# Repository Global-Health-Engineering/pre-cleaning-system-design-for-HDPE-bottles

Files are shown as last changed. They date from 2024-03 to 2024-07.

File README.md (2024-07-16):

<!-- badges: start -->


<!-- badges: end -->

<h1> Design of an HDPE bottle collection and pre-cleaning system for recycling in Blantyre, Malawi </h1>

<b>Contributors</b>  
- Timo Stutz *author*  
- Elizabeth Tilley <a href="https://orcid.org/0000-0002-2095-9724">
ORCID logo 0000-0002-2095-9724
</a> *supervisor*  
- Lin Boynton <a href="https://orcid.org/0000-0002-9944-3834">
ORCID logo 0000-0002-9944-3834
</a> *supervisor*  
- Jakub Tkaczuk <a href="https://orcid.org/0000-0001-7997-9423">
ORCID logo 0000-0001-7997-9423
</a> *supervisor, developer, maintainer*  
- Nicolas Seemann-Ricard <a href="https://orcid.org/0000-0002-0945-7475">
ORCID logo 0000-0002-0945-7475
</a> *developer*  

<br>
<p align="middle"> 

<br><br>
This work is certified by the Open Source Hardware Association.<br \>

<br>
<b>Complete description of system design, functionalities, operation, and maintenance is available on:<br \>
<a href="https://global-health-engineering.github.io/pre-cleaning-system-design-for-HDPE-bottles/">Github pages</a>.
</b>
<br><br>
It compliments the openly-accessible master’s thesis, available on the<br \>  
<a href="https://doi.org/10.3929/ethz-b-000658745">ETH Research Collection</a>.
<br><br>
The pdf version of this repository is available in the <code>report</code> directory of this repo.
</p>

# Background

This repository contains an overview of a prototype for an HDPE bottle pre-cleaning station, developed as a sustainable solution to enhance recycling processes in low-resource settings. The prototype was developed within the master’s thesis of Timo Stutz, contributing to a PhD project conducted by Lin Boynton at the Chair of [Global Health Engineering](https://ghe.ethz.ch/) at [ETH Zurich](https://ethz.ch/en.html). The PhD research aims to design, implement, and evaluate a closed-loop plastic bottle recycling scheme in low-income countries to efficiently, and effectively manage the flow of waste bottles from consumers into new drinking bottles. The prototype addresses the challenges of recycling contaminated HDPE bottles by introducing an efficient, scalable, and locally adaptable pre-cleaning system aiming to reduce the efforts and costs of subsequent recycling processes. Designed and tested through a collaborative research project, this documentation summarizes the prototype's design, constructional and operational procedures, maintenance of the device, and safety recommendations.

# License

This work is licensed under
[Creative Commons Attribution 4.0 International](https://github.com/Global-Health-Engineering/pre-cleaning-system-design-for-HDPE-bottles/blob/main/LICENSE.md).

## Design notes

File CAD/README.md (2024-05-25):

# cad

The `cad` directory contains CAD files produced as a result of the design process. Their names describe what part of the assembly they model. For more details on the subassemblies, refer to the technical documentation and to the design report. 

## file list

- brush.step
- complete_assembly.step
- cutting_tool.step
- frame_workbench.step
- super_maheu_bottle.step
- truck_rail.step
- water_module.step

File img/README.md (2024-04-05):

# media

The media directory contains images and vector files representing the design and prototype. 

## folders

media 
- doc_figures --> figures used in the main README.md
- additional-media --> other relevant media 
   - functional_decomposition --> functional decomposition SVGs 
   - prototype --> built prototype

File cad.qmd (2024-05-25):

---
title: "CAD"
format: html
---

The following CAD drawings are available in [`cad`](https://github.com/Global-Health-Engineering/pre-cleaning-system-design-for-HDPE-bottles/tree/main/CAD) directory in the [GitHub repository](https://github.com/Global-Health-Engineering/pre-cleaning-system-design-for-HDPE-bottles).

```
    cad
    ├── README.md
    ├── brush.step
    ├── complete_assembly.step
    ├── cutting_tool.step
    ├── frame_workbench.step
    ├── super_maheu_bottle.step
    ├── truck_rail.step
    └── water_module.step
```

| file | description |
| --- | --- |
| `brush.step` | brush drawing for bottle cleaning |
| `complete_assembly.step`  | complete assembly of the HDPE cleaning station |
| `cutting_tool.step` | module for cutting the precleaned bottles |
| `frame_workbench.step` | metal workbench, frame of the station |
| `super_maheu_bottle.step` | CAD model of the HDPE bottle |
| `truck_rail.step` | rail for stacking the cleaned and cut bottles  |
| `water_module.step` | pressure generation module for clean water |

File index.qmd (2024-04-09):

---
title: "Design of the HDPE bottle collection and pre-cleaning system for recycling in Blantyre, Malawi"
format: html
---

<!-- badges: start -->


<!-- badges: end -->

<b>Contributors</b>\
- Timo Stutz *author*\
- Elizabeth Tilley <a href="https://orcid.org/0000-0002-2095-9724">
ORCID logo
0000-0002-2095-9724 </a> *supervisor*\
- Lin Boynton <a href="https://orcid.org/0000-0002-9944-3834">
ORCID logo
0000-0002-9944-3834 </a> *supervisor*\
- Jakub Tkaczuk <a href="https://orcid.org/0000-0001-7997-9423">
ORCID logo
0000-0001-7997-9423 </a> *supervisor, developer, maintainer*\
- Nicolas Seemann-Ricard
<a href="https://orcid.org/0000-0002-0945-7475">
ORCID logo
0000-0002-0945-7475 </a> *developer*

<br>
<p align="middle">

<br><br> This work is certified by the Open Source Hardware
Association.\
(https://certification.oshwa.org/ch000021.html)
</p>

<h1>Table of Contents</h1>

1.  [Introduction](#1-introduction)
2.  [Prototype Overview](#2-prototype-overview)
3.  [Part List](#3-part-list)
4.  [User Manual](#4-user-manual)
    1.  [Prototype Construction](#41-prototype-construction)
    2.  [Prototype Operation](#42-prototype-operation)
    3.  [Maintenance](#43-maintenance)
    4.  [Safety Precautions](#44-safety-precautions)
5.  [License](#5-license)

# 1. Introduction

This technical documentation presents an overview of a prototype for an HDPE bottle pre-cleaning station, developed as a sustainable solution to enhance recycling processes in low-resource settings. The prototype was developed within the master's thesis of Timo Stutz, contributing to a PhD project conducted by Lin Boynton at the Chair of Global Health Engineering at ETH Zurich. The PhD research aims to design, implement, and evaluate a closed-loop plastic bottle recycling scheme in low-income countries to efficiently, and effectively manage the flow of waste bottles from consumers into new drinking bottles. The prototype addresses the challenges of recycling contaminated HDPE bottles by introducing an efficient, scalable, and locally adaptable pre-cleaning system aiming to reduce the efforts and costs of subsequent recycling processes. Designed and tested through a collaborative research project, this documentation summarizes the prototype's design, constructional and operational procedures, maintenance of the device, and safety recommendations.

This repository compliments the openly-accessible master's thesis, available the [ETH research collection](https://doi.org/10.3929/ethz-b-000658745).

# 2. Prototype Overview

The pre-cleaning station was mainly developed to address cleanliness requirements of collected HDPE bottles before they undergo recycling. This prototype is segmented into distinct modules, each designed to fulfill a specific function in the pre-cleaning process. Figure 1 shows the CAD drawing of the complete prototype and its different modules. In Figure 2, the complete assembly of the physical prototype is depicted. Finally, Figure 3 shows a focussed view on the inflation and cleaning interface. Below is a summary of each module and its function within the prototype:

1.  **Inflation Module:** This module is responsible for restoring crushed or deformed bottles to their original shape, making them easier to clean and process. By applying controlled pressure, the inflation module ensures that bottles regain a uniform shape for efficient cleaning.

2.  **Cleaning Module:** Equipped with mechanisms for both internal and external cleaning, this module utilizes water jets and brushes to remove organic contaminants from the bottles

3.  **Water Module:** This module provides the necessary water supply for the cleaning process. It includes a manual pump system that generates water pressure without the need for electricity, highlighting the prototype's adaptability to low-resource settings. As water is pumped into the closed loop system, the pressure of the air trapped inside the tank rises and thus, exerts pressure on the water within the pipes. This pressurized water can then be accessed by the cleaning module.

4.  **Stacking Module:** After the bottles are cleaned, the stacking module allows to organize them into manageable stacks for easy transportation and further processing. This is realized with help of a cutting tool and a metal pole which is used as a transport unit for cut bottles.

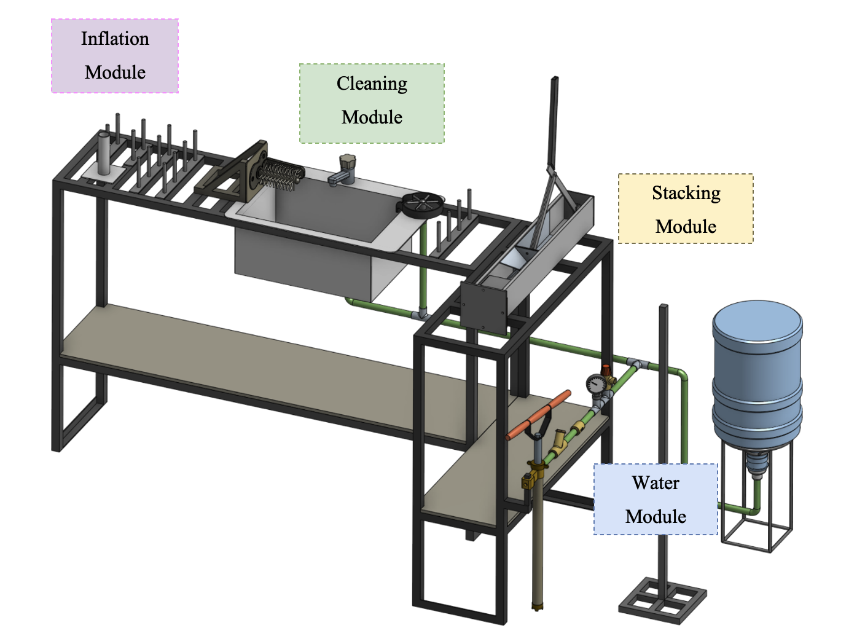
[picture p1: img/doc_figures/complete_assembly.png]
Figure 1: Complete assembly of the pre-cleaning station.


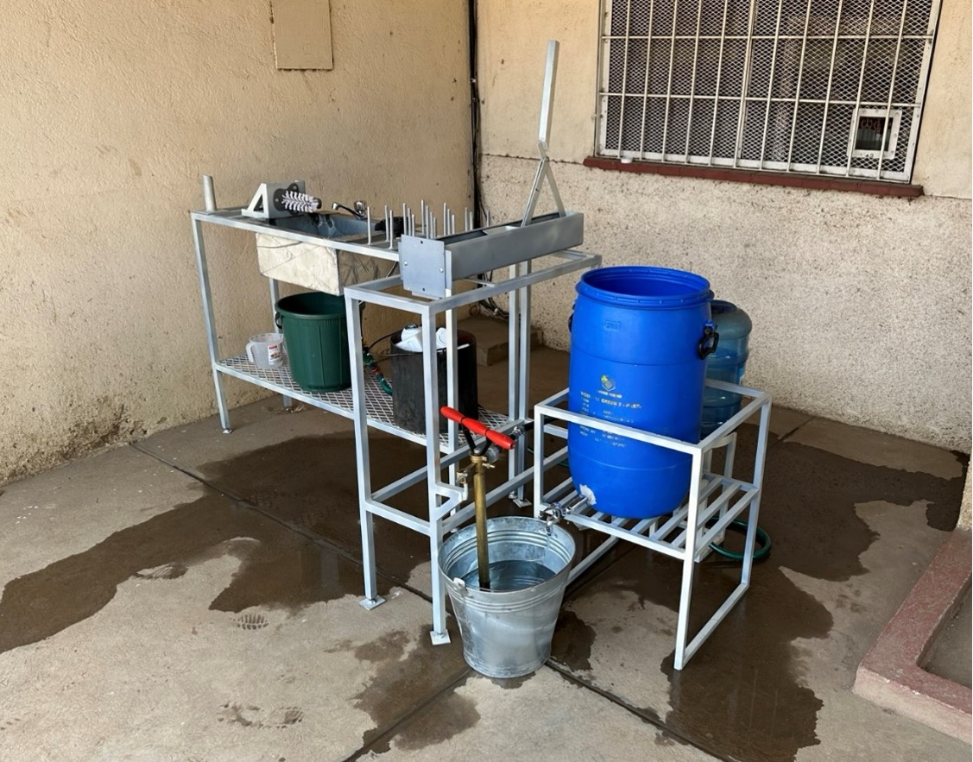
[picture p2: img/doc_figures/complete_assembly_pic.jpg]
Figure 2: Complete assembly of the prototype. All components are included.


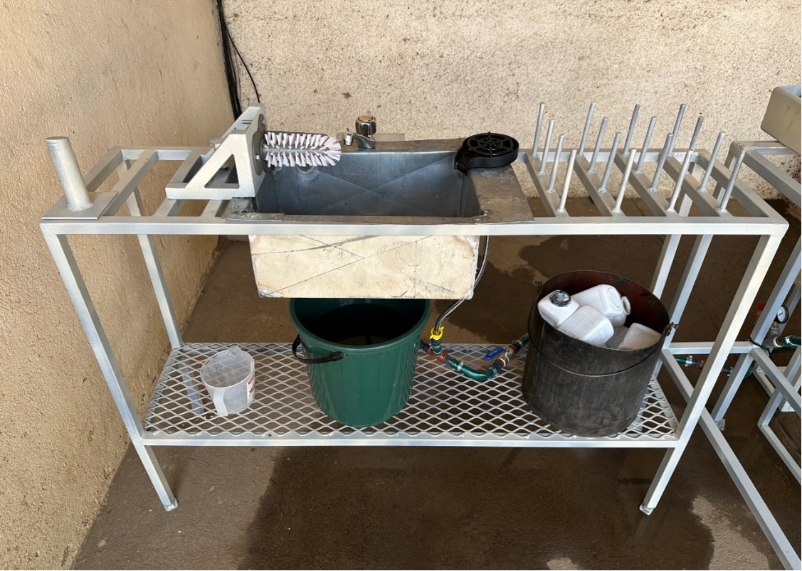
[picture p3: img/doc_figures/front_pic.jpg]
Figure 3: Front view of the inflation and cleaning modules as installed.


# 3. Part List

<p align="center">
Table 1: Part list of the pre-cleaning station in CHF. Where necessary, local prices in MWK were converted into CHF according to the exchange rate at the time of the project.
</p>

| **Module** | **No.** | **Item** | **Specs** | **Qty.** | **Source** | **Price [CHF]** |
|---|:---:|:---:|---|---|---|:---:|
| Workbench | 1 | Square Tube | L x W x H: 20 m x 25 mm x 25 mm | 1 | \*incl. in 41 | |
| Inflation | 2 | Metal Sheet | L x W x H: 10 cm x 10 cm x 3 mm | 1 | \*incl. in 41 | |
| Inflation | 3 | Metal Round Tube | D x L:35 mm x 15 cm | 1 | \*incl. in 41 | |
| Inflation | 4 | Paint | | 1 | Agri-Quip Ltd. | 6 |
| Water | 5 | Double Nipple | 2 x External Thread (ET) G 1 1/2 '' | 1 | D.J. Hardware Ltd. | 2 |
| Water | 6 | Reducing Sleeve | IT G 1 1/2'' to IT G 3/4'' | 1 | D.J. Hardware Ltd. | 3 |
| Water | 7 | T-piece | 3 x IT G 3/4'' | 4 | Van General Dealers | 2 |
| Water | 8 | Ball valve | 2 x IT G 3/4'' | 1 | Van General Dealers | 10 |
| Water | 9 | Hose nipple | ET G 3/4'' to 13 mm | 15 | Phalombe Hardware | 15 |
| Water | 10 | Check valve | 2 x 13 mm | 1 | Temu | 3 |
| Water | 11 | Manometer | 0-3 bar, IT G 1/4'' | 1 | Temu | 5 |
| Water | 12 | Hose | 2 x IT G 3/4'' | 2 | \*incl. in | |
| Water | 13 | Bottle | 20 l | 1 | Sana Cash & Carry | 6 |
| Water | 14 | Water pump | | 1 | Ricardo | 12 |
| Water | 15 | Rubber Hose | D x L: 13 mm x 5 m | 1 | Blantyre Market | 7 |
| Water | 16 | Hose Clamps | 13 mm - 16 mm | 15 | Build Africa Ltd. | 17 |
| Water | 17 | Safety Valve | 2.5 bar | 1 | Bauhaus | 14 |
| Water | 18 | Drum Stand | 60 l | 1 | Ndirande Market | 14 |
| Water | 19 | Metal Bucket | 8 l | 1 | Ndirande Market | 4 |
| Water | 20 | Bottle Stand | | 1 | Steel World & Hardware | 9 |
| Water | 21 | Drum Stand | | 1 | Steel World & Hardware | 13 |
| Water | 22 | Drum Faucet | | 1 | L.R. Hardware | 2 |
| Cleaning | 23 | Rinser | | 1 | Temu | 8 |
| Cleaning | 24 | Sink | Stainless Steel | 1 | Ndirande Market | 28 |
| Cleaning | 25 | Faucet | | 1 | Phalombe Hardware | 13 |
| Cleaning | 26 | Brushes | | 1 | Temu | 5 |
| Cleaning | 27 | Metal Sheet | Thickness 2 - 3 mm | 1 | \*incl. in 41 | |
| Cleaning | 28 | Metal Square Tube | 1 cm x 1 cm | 1 | \*incl. in 41 | |
| Stacking | 29 | Square Tube | W x H x L: 90 mm x 90 mm x 1 m | 1 | \*incl. in 41 | |
| Stacking | 30 | Flat Steel | W x H x L: 20 mm x 4 mm x 1500 mm | 1 | Steel World Ltd. | 13 |
| Stacking | 31 | Rectangular Tube | W x H x L: 25 mm x 12 mm x 300 mm | 1 | \*incl. in 41 | |
| Stacking | 32 | Round Tube | OD 35 mm, L 120 mm | 1 | \*incl. in 41 | |
| Stacking | 33 | Metal Sheet | W x H x L: 500 mm x 4 mm x 300 mm | 1 | \*incl. in 41 | |
| Stacking | 34 | Round Steel (Full Core) | D x L: 10 mm x 3 m | 1 | \*incl. in 41 | |
| Stacking | 35 | Round Tube | OD 35 mm, L 1.5 m | 1 | \*incl. in 40 | |
| Stacking | 36 | Square Tube | For Base | 1 | \*incl. in 40 | |
| Stacking | 37 | Nuts/Bolts | | 1 | Build Africa | 4 |
| Salary Costs | 38 | Bottle Stand | Cutting, Welding, etc. | 1 | Barlows Engineering | 11 |
| Salary Costs | 39 | Drum Stand | Cutting, Welding, etc. | 1 | Barlows Engineering | 27 |
| Salary Costs | 40 | Pole Stand | Cutting, Welding, etc. | 1 | Barlows Engineering | 11 |
| Salary Costs | 41 |  Workbench & Painting | Cutting, Welding, etc. | 1 | Real Steel Industries Ltd. | 337 |
| **Total Costs [CHF]:** | | | | | | **599** |

<br>

# 4. User Manual

## 4.1 Prototype Construction

### **Frame / Workbench**

The construction of the structural frame of the workbench is a crucial step in assembling the HDPE bottle pre-cleaning station prototype. This frame is crafted by welding metal tubes together, forming a sturdy base that supports the various modules of the station. The geometry of the workbench can be adapted according to local requirements and the available space. The width of the frame should be chosen, such that the sink can be inserted. When determining the dimensions of the frame, special attention is given to its height, which is to be selected to ensure comfortable usage (90-100cm).

### **Inflation Module**

The realization of the inflation module is kept as simple as possible and is presented in Figure 4a). The module consists of a round tube welded to a steel plate. The diameter of the tube is approximately 1 cm smaller than the bottle opening to ensure quick and reliable mounting of the bottle. The steel plate is welded to or screwed onto the surface on the workbench below the module.

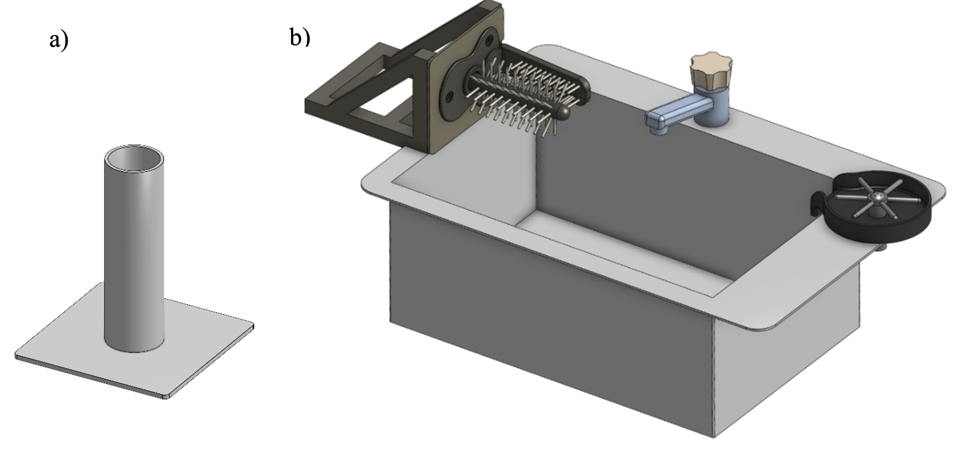
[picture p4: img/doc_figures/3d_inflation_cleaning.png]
Figure 4: 3D-representation of modules: a) Inflation Module, b) Cleaning Module.


### **Cleaning Module**

The cleaning interface depicted in Figure 4b) consists of four primary components. It incorporates a brush, a faucet, a sink, and a glass rinser, each playing a specific role in the cleaning process. Constructing the cleaning module requires planning regarding the placement and installation of the tap and glass rinser. If the sink is being custom manufactured, the design must include holes for both the tap and rinser to ensure a seamless integration. On the other hand, if a pre-made sink is used, an additional hole may need to be drilled to accommodate the glass rinser. In the next step, the sink can be inserted into the workbench allowing to install the tap and rinser. Next, the brush is affixed to a custom holder which can be screwed or welded to the workbench. Since water drops should be captured by the sink, the brush holder is attached last, to ensure that the base of the brush is aligned with the wall of the sink.

### **Water Module**

Figure 5 illustrates the components of the water module. Initially, the placement of the pump and pressure tank must be determined. Following this, a rubber hose is cut to the required length to link all components. Typically, these components are equipped with threaded ends, allowing for the attachment of an threaded hose nipple. The hose is then attached to the components and fastened securely with hose clamps. Adding the clamps is crucial since the system operates under pressure, necessitating a tight and secure connection to prevent leaks and maintain system integrity. The schematic in Figure 5 also displays the order in which the components are installed. In the following a quick functional summary of the different parts is given:

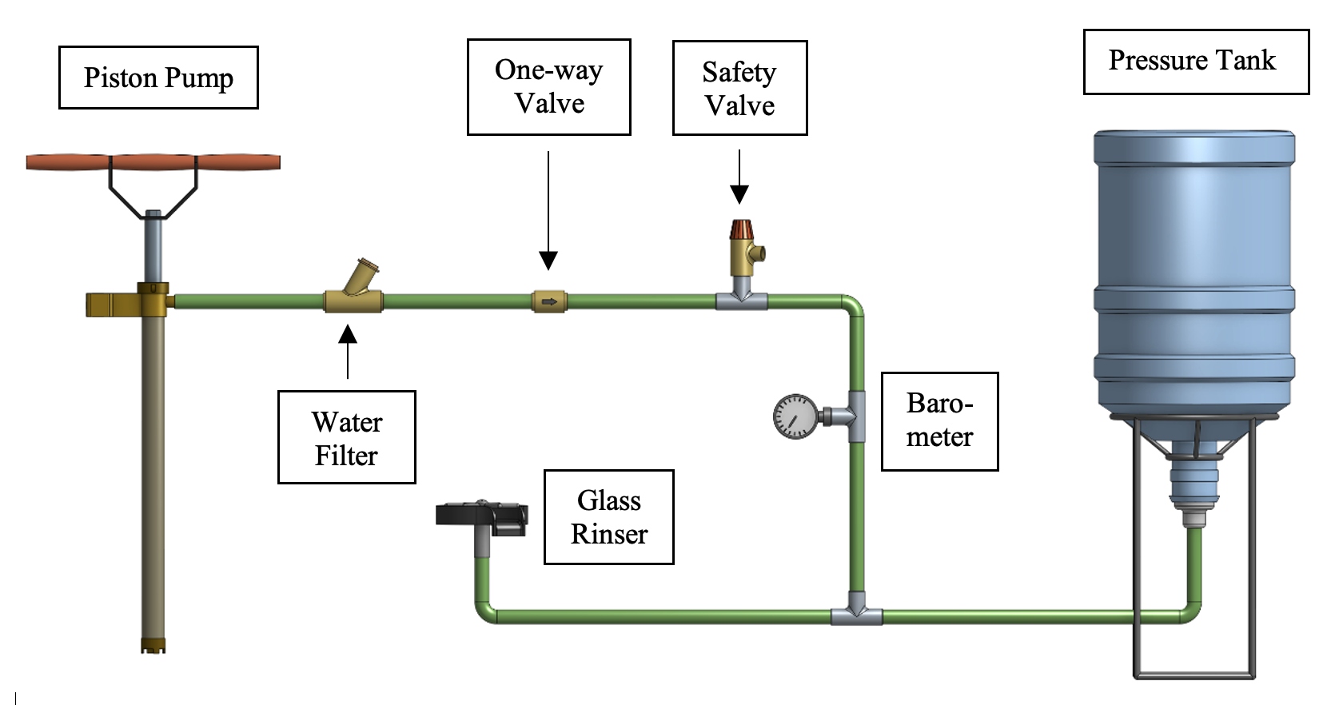
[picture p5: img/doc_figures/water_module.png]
Figure 5: Schematic of the water module utilized to generate water pressure.


- **Manual Piston Pump**: A manual piston pump is used to pump water into the closed system.
- **Dirt Filter**: The water first passes through a dirt filter to remove sand, dirt, and other particles. This filtering process is essential to protect sensitive valves downstream.
- **One-Way Valve**: A one-way valve is used to maintain the generated pressure within the piping system while pumping. This is done by restricting upstream flow through a spring mechanism.
- **Pressure Tank**: The filtered water enters a pressure tank, where the work introduced by the manual pump is converted into air pressure. When the water outlet (glass rinser/tap) is closed, the amount of air particles inside the pressure tank remains constant. As more water is pumped into the closed system, the air inside the pressure tank is compressed, exerting a certain force on the water. This pressure is utilized to operate the glass rinser and tap, even if they are located at a higher position than the pressure tank.
- **Pressure Regulation**: The pre-cleaning setup is designed to work at 2.5 bars of pressure. To ensure worker safety, a barometer to read off current pressure levels, and a pressure-limiting safety valve is included. The spring-loaded mechanism of the safety valve automatically opens if the water pressure inside the pipes exceeds 2.5 bar.
- **Water access**: The water pressure can be accessed through the tap or the glass rinser.

### **Stacking Module**

The bottles are cut using two blades arranged in a cross-like manner. This cutting method allows to bend the walls of the bottle outward while leaving the bottle opening intact. The bottles are then stacked on top of each other onto a pole. As depicted in Figure 6, the cutting tool consists of an outer tube, an inner tube, a cutting interface, and a bottle adapter. The outer and inner tubes are connected via joints, allowing manual operation through a handle. Manually pulling on the lever causes the force to be transmitted through the joints, leading to linear movement of the inner tube. The inner tube acts as a sled for the cutting interface, moving linearly within the outer tube. The cutting interface itself consists of a plate with vertically aligned blades, angled to enhance cutting efficiency.

Construction Steps:

1.  **Prepare the Tubes:** Begin by fixing the dimensions of the outer and inner tubes, ensuring they align correctly for smooth operation. The tubes can be cut out of a single piece of metal tubing and/or angle bars. Attach the top hinge as well as the adapter bracings to opposite ends of the outer tube.
2.  **Assemble the Cutting Interface:** Attach the vertically aligned blades to the horizontal plate. Further weld the bottom hinge to the top side of the plate. This assembly is then welded to the end of the inner tube.
3.  **Install the joint mechanism:** Begin constructing the mechanism by fabricating the handle from metal tubing and cutting three flat bars to the lengths specified (CAD files available in this git repository). Proceed to drill holes at where the joints will be located. Following this, weld the handle to the long flat bar at a right angle (90°). To assemble the mechanism, join its components by screwing them together, ensuring it is securely connected to both the outer tube and the cutting interface.
4.  **Install the Bottle Adapter:** The bottle adapter, crucial for positioning the bottle during the cutting process, attaches to the outer tube with help of 4 screws. The adapter's walls assist in centering the bottle, while a metal tube with vertical cuts welded onto the adapter offers counterpressure, ensuring a clean cut and protecting the user from the blades.
5.  **Add the cutting tool to the workbench:** The cutting tool can be horizontally welded or screwed to the workbench or vertically attached to a wall.

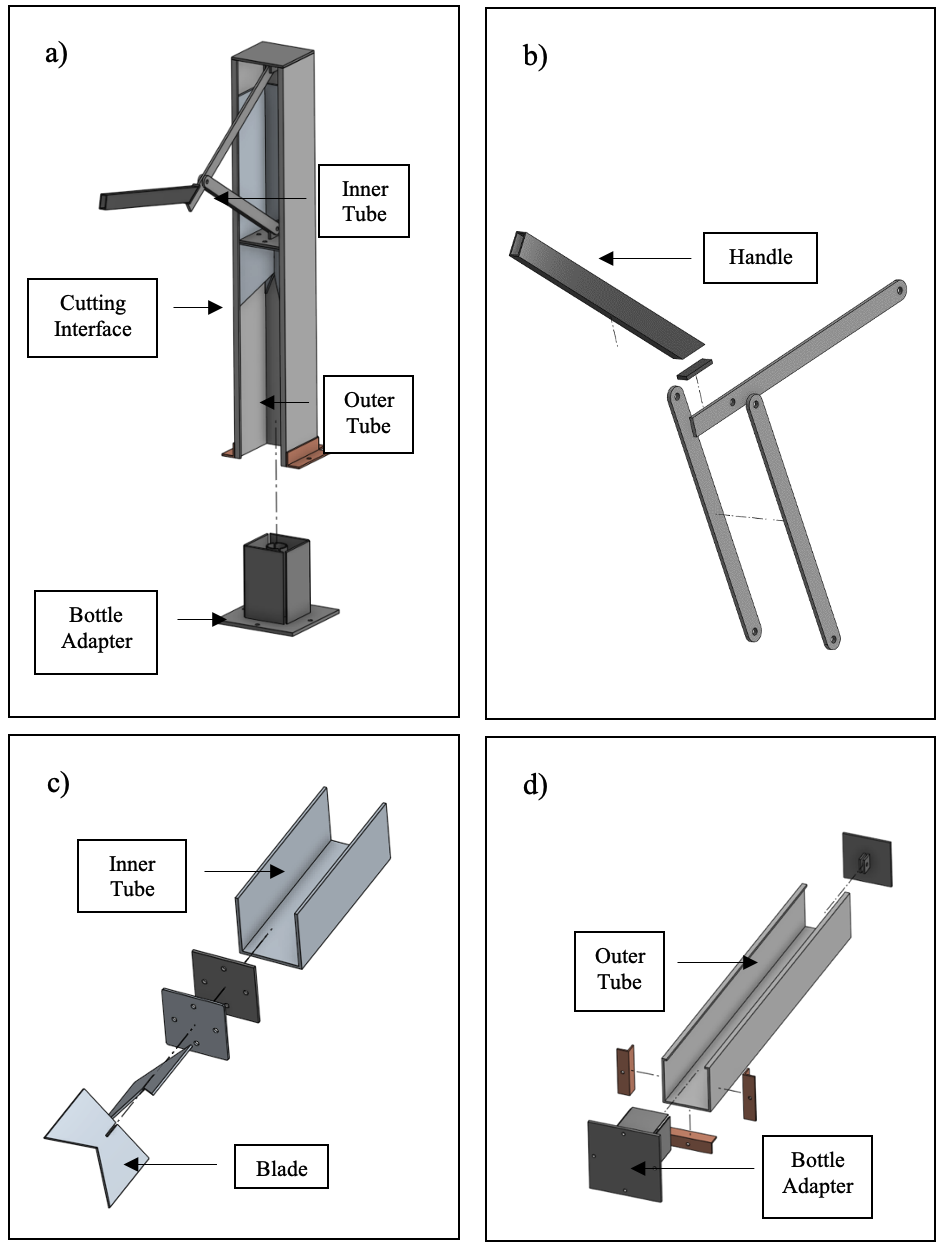
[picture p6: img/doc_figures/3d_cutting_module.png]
Figure 6: 3D- representation of the cutting module: a) Complete Assembly, b) Explosion view of the handle and joints, c) Explosion view of the inner tube with blades attached, d) Explosion view of the outer tube with the bottle adapter attached.


## 4.2 Prototype Operation

This manual leads users through the process of operating the bottle pre-cleaning station. The setup can be used to transform crushed and dirty HDPE bottles into clean, cut, and ready-for-recycling materials.

### **Preparing the setup**

- Start by inserting the pump into a bucket of water and manually operate the handle to generate water pressure within the system. This is achieved by moving the pump handle in a back-and-forth motion until the desired pressure, indicated by the barometer, is reached.
- Make sure that the safety valve is properly functional by twisting the red cap. It is important to always have an eye on the pressure gauge to see whether the pressure is within limits or dropped over time.
- After a certain period of using the pressurized water, the manual pump needs to be re-operated to reach the desired pressure level again.

### **Sorting and Inspection**

Sort the HDPE bottles, and remove any items placed within. Inspect each bottle for excessive damage that could hinder the cleaning process.

### **Inflation**

In case a bottle is crushed, mount it onto the inflation module and manually wiggle the bottle around the vertical tube to inflate it back to its original shape.

### **Removal of material contaminants and soaking**

Remove the bottle's lid and label by peeling them off the bottle. If necessary, use a knife or a sharp edge to start loosening the label before peeling it off. Once the material contaminants are removed, put a first batch of bottles into a bucket of water to soak the entire surface of the bottle, reducing the workload of the main cleaning steps. Soaked in water for a minute, the bottles are ready for the next steps.

### **Cleaning and Drying**

Quickly rinse the bottle under the tap to remove loose dirt and debris. Press the bottle upside-down onto the glass rinser and use the manual brush to thoroughly clean both the interior and exterior of the bottle.

This step may need to be repeated a couple of times in case of heavily soiled bottles. Once the bottles are clean, place the cleaned bottles onto the vertical pins to allow excess water to drip out before cutting. The rinsing step as well as the temporary bottle storage are visualized in Figure 7.

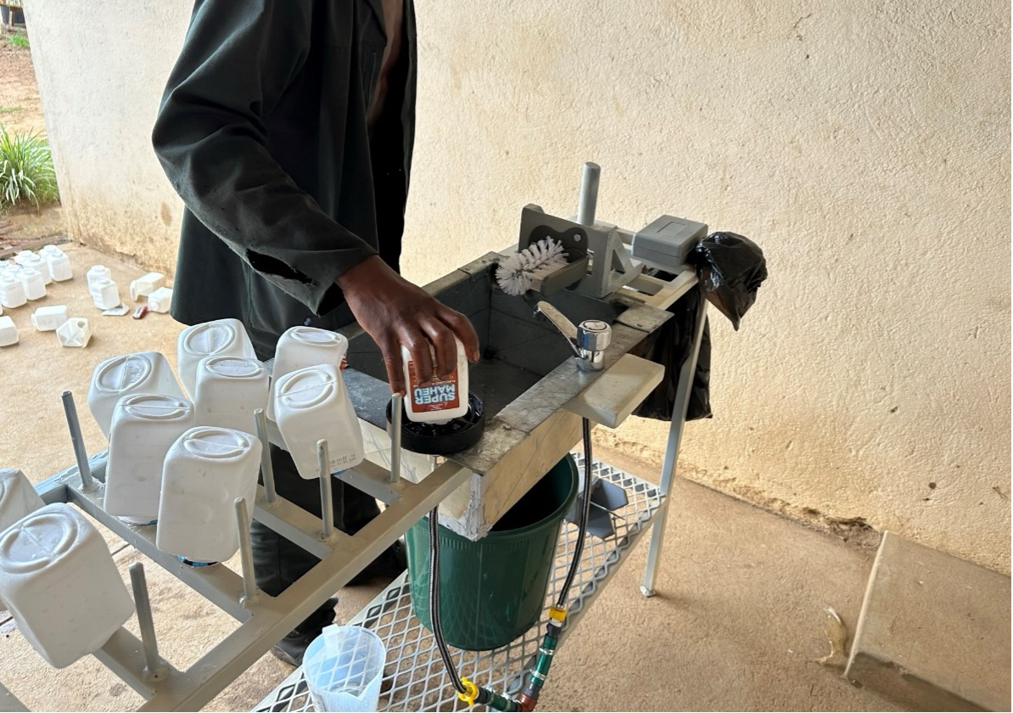
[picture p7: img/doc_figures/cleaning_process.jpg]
Figure 7: Cleaning Process of HDPE bottles. The vertical pins act as temporary storage of cleaned bottles.


### **Cutting**

Once the bottle is clean and dry, place it into the stacking module. Place the bottle into the adapter and manually operate the handle to activate the cutting tool. The blades, arranged in a cross-like manner, should cut the bottle while preserving the opening intact. This process prepares the bottle for efficient stacking.

### **Inspection and Storage**

Inspect the cut and cleaned bottle for any missed contaminants, and if necessary, remove the remains. Place the bottles through the opening onto the transport unit (pole) as represented in Figure 8.

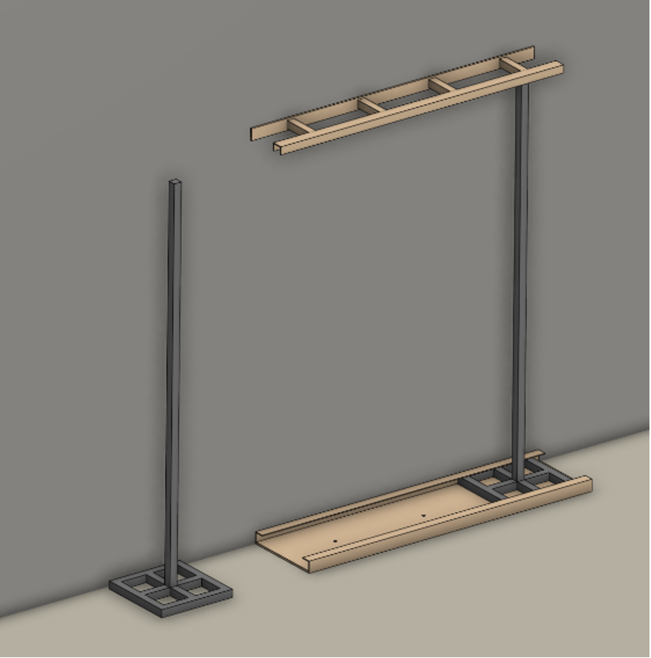
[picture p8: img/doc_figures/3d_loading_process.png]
Figure 8: 3D-representation of the loading process. Bottles are stacked on the pole and slide into the rail.


## 4.3 Maintenance

To maintain the efficiency and longevity of the bottle pre-cleaning station, adhere to the following maintenance routines. Regular maintenance also contributes to a safer working environment for all operators.

- **Regular Inspection:** Conduct routine inspections of all modules, focusing on wear and tear, especially on the moving parts, hoses, and joints. Check for any signs of damage or corrosion that could impact the station's functionality. If necessary tighten screws that were loosened over time.
- **Water Module Maintenance:** The filters in the water module should be cleaned and checked for clogs regularly to maintain optimal water flow and pressure. Inspect the pump and valves for signs of wear or leakage and replace parts as necessary.
- **Cutting Tool Care:** Regularly inspect the cutting blades for sharpness and signs of wear. Dull blades can result in inefficient cutting and restricted functionality. Resharpen or replace blades when a significant decrease in performance is noticed.
- **Pressure Tank Inspection:** Periodically inspect the pressure tank for any signs of damage, corrosion, or wear. Check the seals and valves to ensure they are functioning correctly and not leaking. It's crucial to maintain the tank properly to prevent potential safety hazards due to overpressure or material failure.

## 4.4 Safety Precautions

Operating the HDPE Bottle Pre-Cleaning Station involves various components that require careful handling to ensure safety. Pay special attention to the following:

- **Protective Gear:** Always wear appropriate protective gear, including gloves, eyewear, and closed-toe shoes, to safeguard against potential hazards such as splashes, sharp
edges, or falling tools.
- **Handling Sharp Edges:** The cutting tool incorporates sharp blades that pose a risk of cuts or injuries. Handle the cutting module with utmost care, especially when inserting or removing bottles from the adapter. Ensure the blades are fully retracted when performing maintenance or adjustments.
- **Monitoring Water Pressure:** The pressure tank is a critical component of the cleaning module. Regularly check the tank's integrity and the pressure levels during operation using the barometer and a visual check on deformed parts or leakage. Ensure that the pressure stays within the recommended safety limits to prevent any risk of tank rupture or leaks. For this reason do not operate the pre-cleaning station without a safety valve.
- **Secure Operation Area:** Keep the operational area around the pre-cleaning station clear of clutter, water, and cleaning agents to prevent slips and falls. Ensure that all pipes and hoses are properly managed to avoid tripping hazards.

# 5. License

The complete design and user manual are licensed under [Creative Commons Attribution 4.0 International](https://github.com/Global-Health-Engineering/pre-cleaning-system-design-for-HDPE-bottles/blob/main/LICENSE.md).

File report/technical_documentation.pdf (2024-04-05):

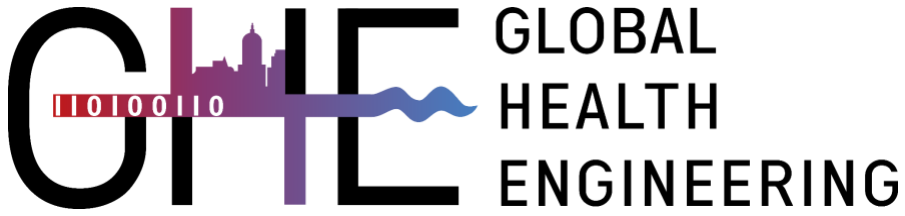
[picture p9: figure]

## Design of an HDPE bottle collection and pre-cleaning system for recycling in Blantyre, Malawi

# Technical Documentation

Author: | Timo Stutz
Supervisors: | Prof. Dr. Elizabeth Tilley Dr. Jakub Tkaczuk Lin Boynton

07-03-2024

## Table of Contents

1 | Introduction | 3
2 | Prototype Overview | 3
3 | Part List | 6
4 | User Manual | 8
| 4.1 Prototype Construction | 8
| 4.2 Prototype Operation | 12
| 4.3 Maintenance | 15
| 4.4 Safety Precautions | 15

## 1 Introduction

This technical documentation presents an overview of a prototype for an HDPE bottle pre-

cleaning station, developed as a sustainable solution to enhance recycling processes in low-re-

source settings. The prototype was developed within the master’s thesis of Timo Stutz, contrib-

uting to a PhD project conducted by Lin Boynton at the Chair of Global Health Engineering at

ETH Zurich. The PhD research aims to design, implement, and evaluate a closed-loop plastic

bottle recycling scheme in low-income countries to efficiently, and effectively manage the flow

of waste bottles from consumers into new drinking bottles. The prototype addresses the challenges

of recycling contaminated HDPE bottles by introducing an efficient, scalable, and locally adapt-

able pre-cleaning system aiming to reduce the efforts and costs of subsequent recycling processes.

Designed and tested through a collaborative research project, this documentation summarizes the

prototype's design, constructional and operational procedures, maintenance of the device, and

safety recommendations.

The underlying master’s thesis is openly accessible on the ETH Zurich research collection

and can be found with help of the link below. Further, the prototype documentation and CAD

drawings can be accessed on the corresponding GitHub repository (linked on the research collec-

tion):

Link: https://www.research-collection.ethz.ch/handle/20.500.11850/658745

## 2 Prototype Overview

The pre-cleaning station was mainly developed to address cleanliness requirements of col-

lected HDPE bottles before they undergo recycling. This prototype is segmented into distinct

modules, each designed to fulfill a specific function in the pre-cleaning process. Figure 1 shows

the CAD drawing of the complete prototype and its different modules. In Figure 2, the complete

assembly of the physical prototype is depicted. Finally, Figure 3 shows a focussed view on the

inflation and cleaning interface. Below is a summary of each module and its function within the

prototype:

1. Inflation Module: This module is responsible for restoring crushed or deformed bottles to

their original shape, making them easier to clean and process. By applying controlled pres-

sure, the inflation module ensures that bottles regain a uniform shape for efficient cleaning.

2. Cleaning Module: Equipped with mechanisms for both internal and external cleaning, this

module utilizes water jets and brushes to remove organic contaminants from the bottles

3. Water Module: This module provides the necessary water supply for the cleaning process.

It includes a manual pump system that generates water pressure without the need for elec-

tricity, highlighting the prototype's adaptability to low-resource settings. As water is

pumped into the closed loop system, the pressure of the air trapped inside the tank rises and

thus, exerts pressure on the water within the pipes. This pressurized water can then be ac-

cessed by the cleaning module.

4. Stacking Module: After the bottles are cleaned, the stacking module allows to organize

them into manageable stacks for easy transportation and further processing. This is realized

with help of a cutting tool and a metal pole which is used as a transport unit for cutt bottles.

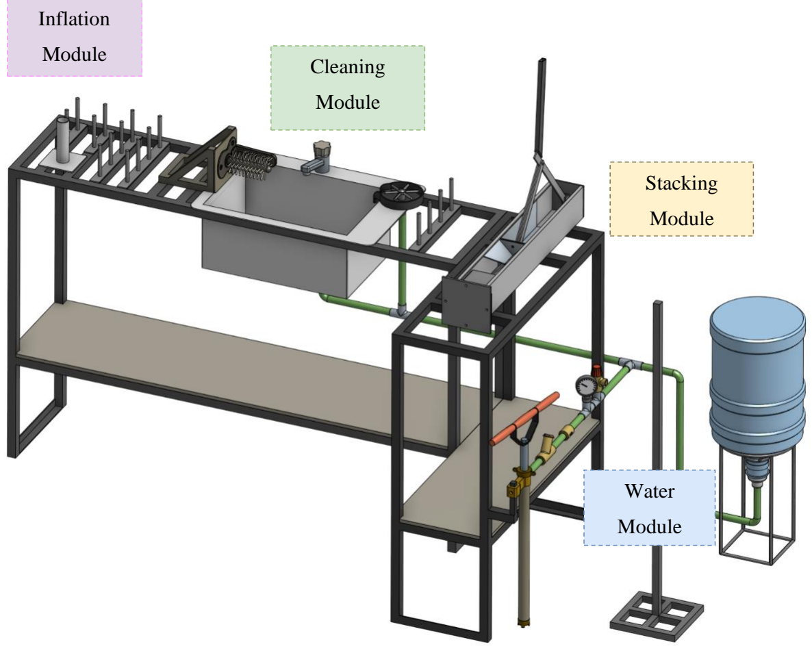
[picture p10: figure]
Water; Module; Inflation; Cleaning; Stacking

Figure 1: Complete assembly of the pre-cleaning station

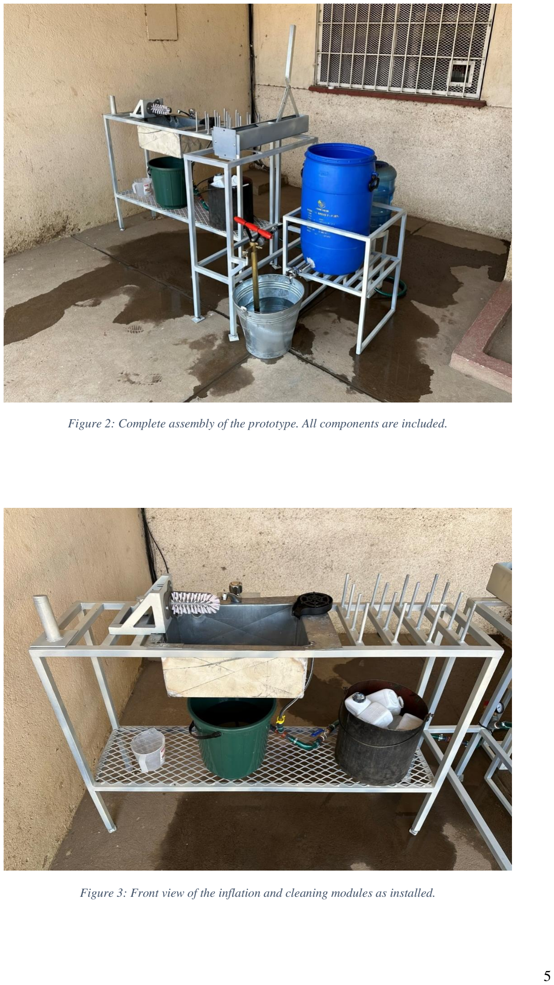
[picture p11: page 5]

Figure 3: Front view of the inflation and cleaning modules as installed.

Figure 2: Complete assembly of the prototype. All components are included.

## 3 Part List

Module | No. | Item | Specs | Qty. Source

Price
(CHF)
Work- bench | 1 | Square Tube | L x W x H: 20m x 25mm x 25mm
1 | *incl. in 41
Inflation | 2 | Metal Sheet | L x W x H: 10cm x
10 cm x 3mm
| | | 1 | *incl. in 41
3 | Metal Round Tube | D x L: 35mm x 15cm | 1 | *incl. in 41
4 | Paint | | 1 | Agri-Quip Ltd. | 6
Water | 5 | Double
| Nipple | 2x External Thread (ET) G 1 1/2 '' | 1 | D.J. Hardware Ltd. | 2
6 | Reducing Sleeve | IT G 1 1/2'' to IT G 3/4'' | 1 | D.J. Hardware Ltd. | 3
7 | T-piece | 3x IT G 3/4'' | 4 | Van General Dealers | 2
8 | Ball valve | 2x IT G 3/4'' | 1 | Van General Dealers | 10
9 | Hose nipple | ET G 3/4'' to 13mm | 15 | Phalombe Hard- ware | 15
10 | Check valve | 2x 13mm | 1 | Temu | 3
11 | Manometer | 0-3 bar, IT G 1/4'' | 1 | Temu | 5
12 | Hose | 2x IT G 3/4'' | 2 | *incl. in
13 | Bottle | 20L | 1 | Sana Cash & Carry | 6
14 | Water pump | | 1 | Ricardo | 12
15 | Rubber Hose | D x L: 13mm x 5m | 1 | Blantyre Market | 7
16 | Hose Clamps 13mm-16mm | 15 | Build Africa Ltd. | 17
17 | Safety Valve | 2.5bar | 1 | Bauhaus | 14
18 | Drum Stand | 60L | 1 | Ndirande Market | 14
19 | Metal Bucket 8L | 1 | Ndirande Market | 4
20 | Bottle Stand | | 1 | Steel World & Hardware | 9
21 | Drum Stand | | 1 | Steel World & Hardware | 13
22 | Drum Faucet | | 1 | L.R. Hardware | 2

Table 1: Part List of Pre-Cleaning Station. Where necessary, local prices in MWK were converted into CHF according to the exchange at the time of the project.

Cleaning 23 | Rinser | | 1 | Temu | 8
24 | Sink | Stainless Steel | 1 | Ndirande Market | 28
25 | Faucet | | 1 | Phalombe Hardware | 13
26 | Brushes | | 1 | Temu | 5
27 | Metal Sheet | Thickness 2-3 mm | 1 | *incl. in 41
28 | Metal Square Tube | 1cmx1cm | 1 | *incl. in 41
Stacking 29 | Square Tube | WxHxL: 90mm x 90mm x 1m | 1 | *incl. in 41
30 | Flat Steel | WxHxL: 20mm x 4mm x 1500mm | 1 | Steel World Ltd. | 13
31 | Rectangular Tube | WxHxL: 25mm x 12mm x 300mm | 1 | *incl. in 41
32 | Round Tube | OD 35mm, L 120mm | 1 | *incl. in 41
33 | Metal Sheet | WxHxL: 500mm x 4mm x 300mm | 1 | *incl. in 41
34 | Round Steel (Full Core) | D x L: 10mm x 3m | 1 | *incl. in 41
35 | Round Tube | OD 35mm, L 1.5m | 1 | *incl. in 40
36 | Square Tube | For Base | 1 | *incl. in 40
37 | Nuts/Bolts | | 1 | Build Africa | 4

Salary
Costs
38 | Bottle Stand | Cutting, Welding, etc. | 1 | Barlows Engineering | 11
39 | Drum Stand | Cutting, Welding, etc. | 1 | Barlows Engineering | 27
40 | Pole Stand | Cutting, Welding, etc. | 1 | Barlows Engineering | 11
41 | Workbench & Painting | Cutting, Welding, etc. | 1 | Real Steel Industries Ltd. | 337
Total Costs Prototype (CHF): | 599

Table 2(continued): Part list of the pre-cleaning station in CHF. Where necessary, local prices in MWK were converted into CHF according to the exchange at the time of the project.

## 4 User Manual

## 4.1 Prototype Construction

Frame / Workbench

The construction of the structural frame of the workbench is a crucial step in assembling

the HDPE bottle pre-cleaning station prototype. This frame is crafted by welding metal tubes

together, forming a sturdy base that supports the various modules of the station. The geometry of

the workbench can be adapted according to local requirements and the available space. The width

of the frame should be chosen, such that the sink can be inserted. When determining the dimen-

sions of the frame, special attention is given to its height, which is to be selected to ensure com-

fortable usage (90-100cm).

Inflation Module

The realization of the inflation module is kept as simple as possible and is presented in

Figure 4a). The module consists of a round tube welded to a steel plate. The diameter of the tube

is approximately 1cm smaller than the bottle opening to ensure quick and reliable mounting of

the bottle. The steel plate is welded to or screwed onto the surface on the workbench below the

module.

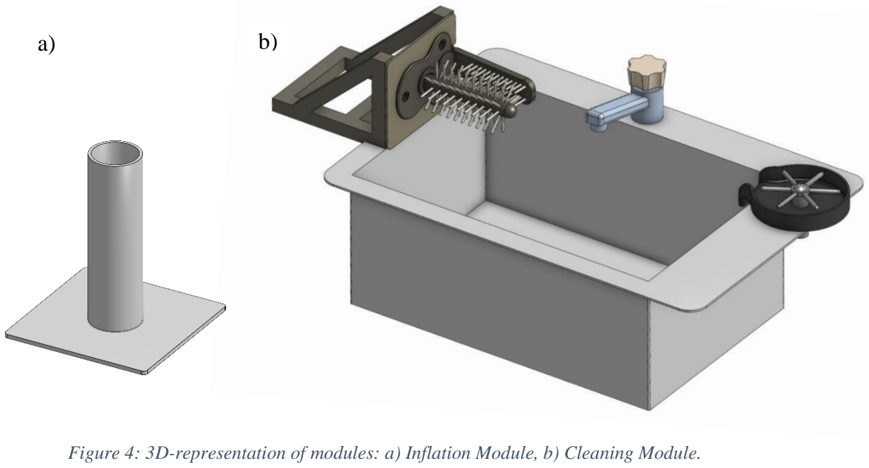
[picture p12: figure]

Figure 4: 3D-representation of modules: a) Inflation Module, b) Cleaning Module.

Cleaning Module

The cleaning interface depicted in Figure 4b) consists of four primary components. It in-

corporates a brush, a faucet, a sink, and a glass rinser, each playing a specific role in the cleaning

process. Constructing the cleaning module requires planning regarding the placement and instal-

lation of the tap and glass rinser. If the sink is being custom manufactured, the design must include

holes for both the tap and rinser to ensure a seamless integration. On the other hand, if a pre-made

sink is used, an additional hole may need to be drilled to accommodate the glass rinser. In the

next step, the sink can be inserted into the workbench allowing to install the tap and rinser. Next,

the brush is affixed to a custom holder which can be screwed or welded to the workbench. Since

water drops should be captured by the sink, the brush holder is attached last, to ensure that the

base of the brush is aligned with the wall of the sink.

Water Module

Figure 5 illustrates the components of the water module. Initially, the placement of the

pump and pressure tank must be determined. Following this, a rubber hose is cut to the required

length to link all components. Typically, these components are equipped with threaded ends, al-

lowing for the attachment of an threaded hose nipple. The hose is then attached to the components

and fastened securely with hose clamps. Adding the clamps is crucial since the system operates

under pressure, necessitating a tight and secure connection to prevent leaks and maintain system

integrity. The schematic in Figure 5 also displays the order in which the components are installed.

In the following a quick functional summary of the different parts is given:

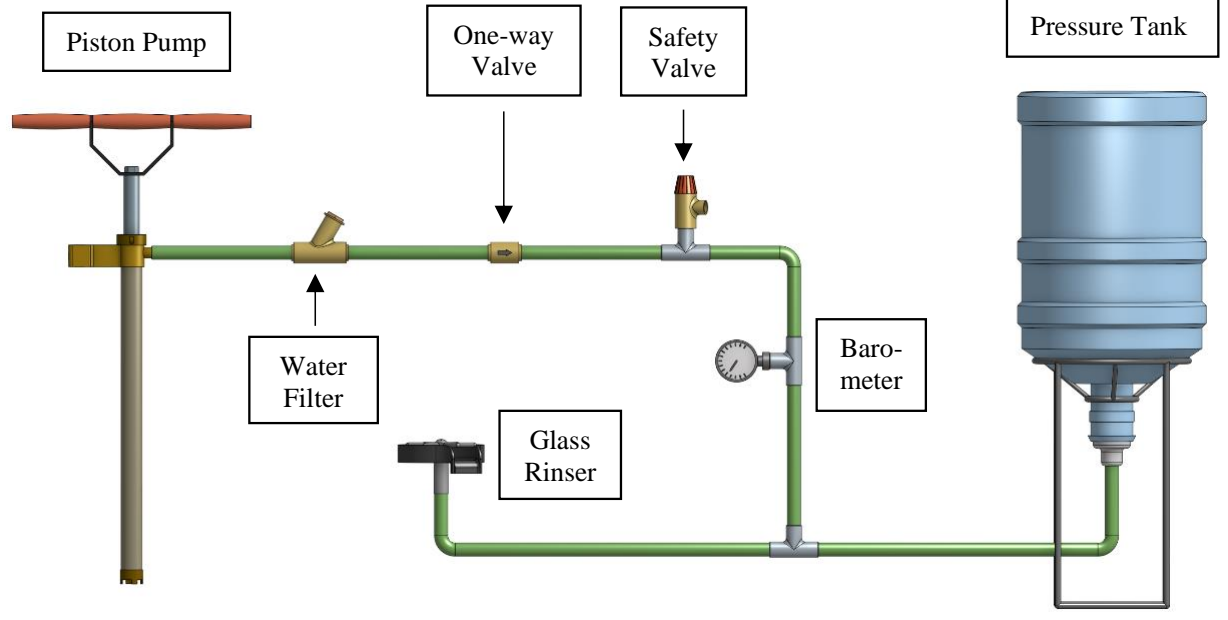
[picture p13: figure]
Piston Pump; Water Filter; One-way Valve; Safety Valve; Baro- meter; Glass Rinser; Pressure Tank

Figure 5: Schematic of the water module utilized to generate water pressure..

- Manual Piston Pump: A manual piston pump is used to pump water into the closed sys-

tem.

- Dirt Filter: The water first passes through a dirt filter to remove sand, dirt, and other par-

ticles. This filtering process is essential to protect sensitive valves downstream.

- One-Way Valve: A one-way valve is used to maintain the generated pressure within the

piping system while pumping. This is done by restricting upstream flow through a spring

mechanism.

- Pressure Tank: The filtered water enters a pressure tank, where the work introduced by

the manual pump is converted into air pressure. When the water outlet (glass rinser/tap) is

closed, the amount of air particles inside the pressure tank remains constant. As more water

is pumped into the closed system, the air inside the pressure tank is compressed, exerting a

certain force on the water. This pressure is utilized to operate the glass rinser and tap, even

if they are located at a higher position than the pressure tank.

- Pressure Regulation: The pre-cleaning setup is designed to work at 2.5 bars of pressure.

To ensure worker safety, a barometer to read off current pressure levels, and a pressure-

limiting safety valve is included. The spring-loaded mechanism of the safety valve auto-

matically opens if the water pressure inside the pipes exceeds 2.5 bars.

- Water access: The water pressure can be accessed through the tap or the glass rinser.

Stacking Module

The bottles are cut using two blades arranged in a cross-like manner. This cutting method

allows to bend the walls of the bottle outward while leaving the bottle opening intact. The bottles

are then stacked on top of each other onto a pole. As depicted in Figure 6, the cutting tool consists

of an outer tube, an inner tube, a cutting interface, and a bottle adapter. The outer and inner tubes

are connected via joints, allowing manual operation through a handle. Manually pulling on the

lever causes the force to be transmitted through the joints, leading to linear movement of the inner

tube. The inner tube acts as a sled for the cutting interface, moving linearly within the outer tube.

The cutting interface itself consists of a plate with vertically aligned blades, angled to enhance

cutting efficiency.

Construction Steps:

1. Prepare the Tubes: Begin by fixing the dimensions of the outer and inner tubes, ensuring

they align correctly for smooth operation. The tubes can be cut out of a single piece of

metal tubing and/or angle bars. Attach the top hinge as well as the adapter bracings to

opposite ends of the outer tube.

2. Assemble the Cutting Interface: Attach the vertically aligned blades to the horizontal

plate. Further weld the bottom hinge to the top side of the plate. This assembly is then

welded to the end of the inner tube.

3. Install the joint mechanism: Begin constructing the mechanism by fabricating the han-

dle from metal tubing and cutting three flat bars to the lengths specified (CAD files avail-

able in the Git repository). Proceed to drill holes at where the joints will be located. Fol-

lowing this, weld the handle to the long flat bar at a right angle (90°). To assemble the

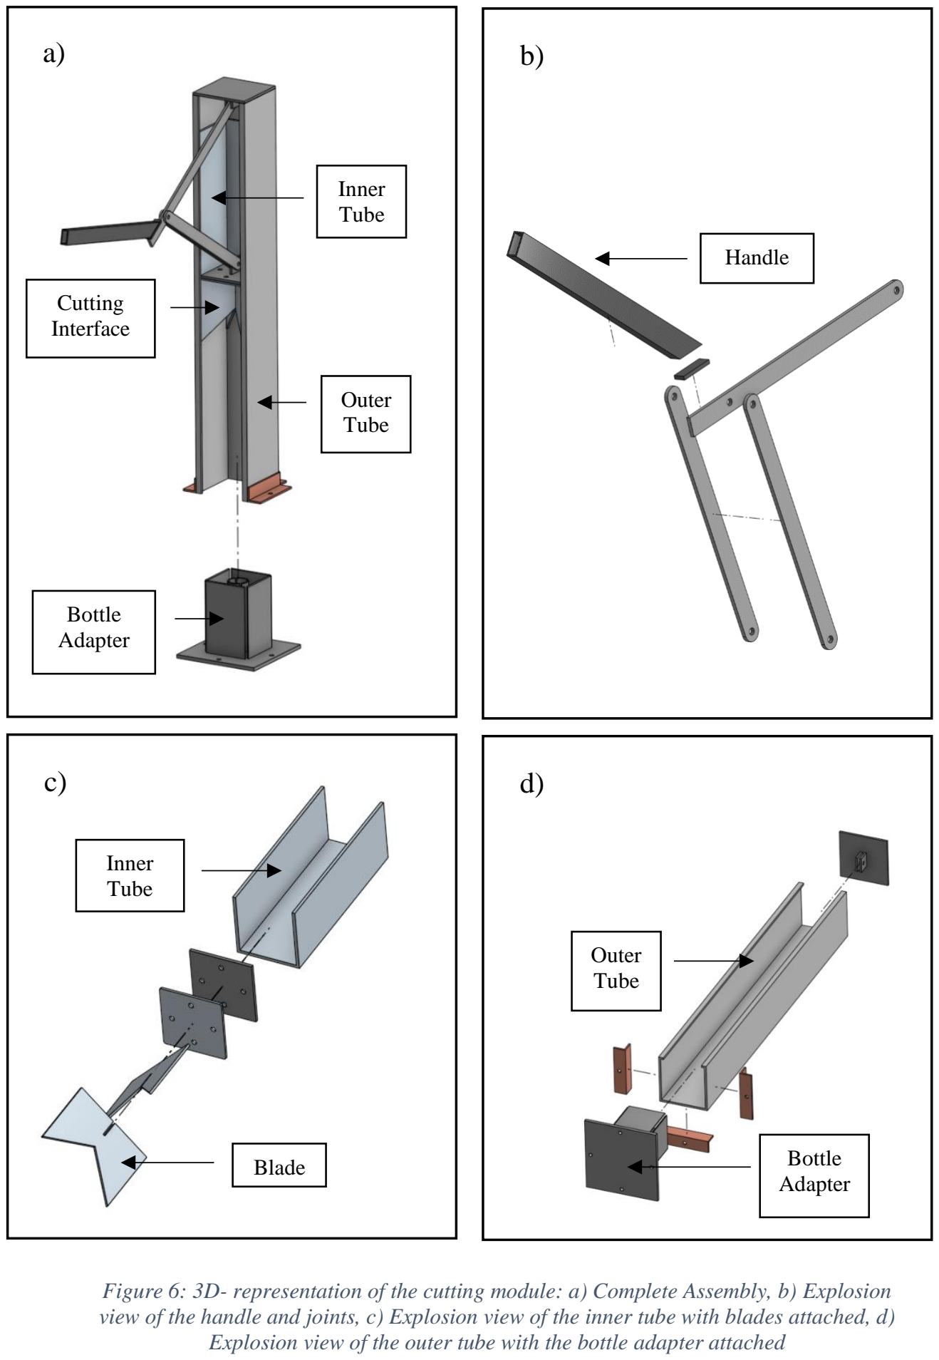
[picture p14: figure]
Outer Tube; Inner Tube; Bottle Adapter; Cutting Interface; Handle; Blade

Figure 6: 3D- representation of the cutting module: a) Complete Assembly, b) Explosion view of the handle and joints, c) Explosion view of the inner tube with blades attached, d) Explosion view of the outer tube with the bottle adapter attached mechanism, join its components by screwing them together, ensuring it is securely con-

nected to both the outer tube and the cutting interface.

4. Install the Bottle Adapter: The bottle adapter, crucial for positioning the bottle during

the cutting process, attaches to the outer tube with help of 4 screws. The adapter's walls

assist in centering the bottle, while a metal tube with vertical cuts welded onto the adapter

offers counterpressure, ensuring a clean cut and protecting the user from the blades.

5. Add the cutting tool to the workbench: The cutting tool can be horizontally welded or

screwed to the workbench or vertically attached to a wall.

## 4.2 Prototype Operation

This manual leads users through the process of operating the bottle pre-cleaning station.

The setup can be used to transform crushed and dirty HDPE bottles into clean, cut, and ready-for-

recycling materials.

Preparing the setup:

- Start by inserting the pump into a bucket of water and manually operate the handle to

generate water pressure within the system. This is achieved by moving the pump handle

in a back-and-forth motion until the desired pressure, indicated by the barometer, is

reached.

- Make sure that the safety valve is properly functional by twisting the red cap. It is im-

portant to always have an eye on the pressure gauge to see whether the pressure is within

limits or dropped over time.

- After a certain period of using the pressurized water, the manual pump needs to be re-

operated to reach the desired pressure level again.

Sorting and Inspection:

Sort the HDPE bottles, and remove any items placed within. Inspect each bottle for excessive

damage that could hinder the cleaning process.

Inflation:

In case a bottle is crushed, mount it onto the inflation module and manually wiggle the bottle

around the vertical tube to inflate it back to its original shape.

Removal of material contaminants and soaking:

Remove the bottle's lid and label by peeling them off the bottle. If necessary, use a knife or a

sharp edge to start loosening the label before peeling it off. Once the material contaminants

are removed, put a first batch of bottles into a bucket of water to soak the entire surface of the

bottle, reducing the workload of the main cleaning steps. Soaked in water for a minute, the

bottles are ready for the next steps.

Cleaning and Drying:

Quickly rinse the bottle under the tap to remove loose dirt and debris. Press the bottle upside-

down onto the glass rinser and use the manual brush to thoroughly clean both the interior and

exterior of the bottle.

This step may need to be repeated a couple of times in case of heavily soiled bottles. Once

the bottles are clean, place the cleaned bottles onto the vertical pins to allow excess water to

drip out before cutting. The rinsing step as well as the temporary bottle storage are visualized

in Figure 7.

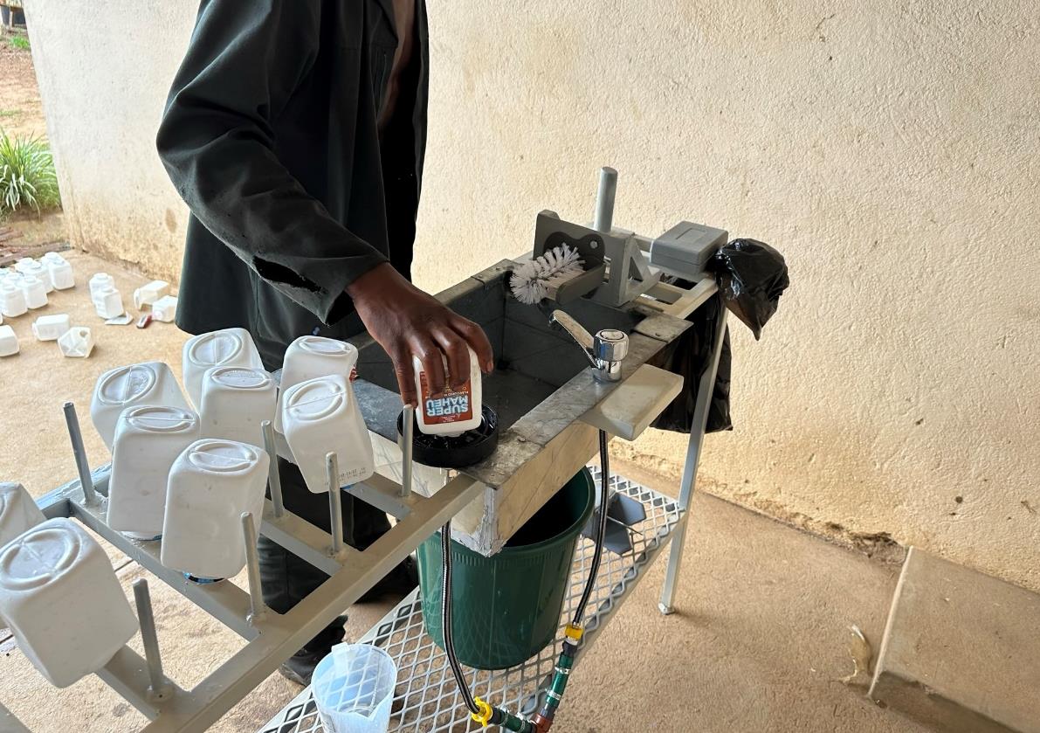
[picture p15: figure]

Figure 7: Cleaning Process of HDPE bottles. The vertical pins act as temporal storage of cleaned

Cutting:

Once the bottle is clean and dry, place it into the stacking module. Place the bottle into the adapter

and manually operate the handle to activate the cutting tool. The blades, arranged in a cross-like

manner, should cut the bottle while preserving the opening intact. This process prepares the bottle

for efficient stacking.

Inspection and Storage:

Inspect the cut and cleaned bottle for any missed contaminants, and if necessary, remove the

remains. Place the bottles through the opening onto the transport unit (pole) as represented in

Figure 8.

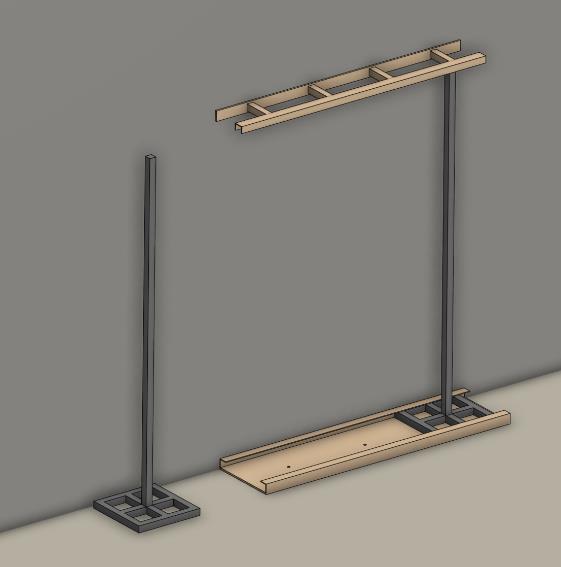
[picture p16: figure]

Figure 8: 3D-representation of the loading process. Bottles are stacked on the pole and slide into the rail

## 4.3 Maintenance

To maintain the efficiency and longevity of the bottle pre-cleaning station, adhere to the

following maintenance routines. Regular maintenance also contributes to a safer working envi-

ronment for all operators.

- Regular Inspection: Conduct routine inspections of all modules, focusing on wear and

tear, especially on the moving parts, hoses, and joints. Check for any signs of damage or

corrosion that could impact the station's functionality. If necessary tighten screws that

were loosened over time.

- Water Module Maintenance: The filters in the water module should be cleaned and

checked for clogs regularly to maintain optimal water flow and pressure. Inspect the

pump and valves for signs of wear or leakage and replace parts as necessary.

- Cutting Tool Care: Regularly inspect the cutting blades for sharpness and signs of

wear. Dull blades can result in inefficient cutting and restricted functionality. Resharpen

or replace blades when a significant decrease in performance is noticed.

- Pressure Tank Inspection: Periodically inspect the pressure tank for any signs of dam-

age, corrosion, or wear. Check the seals and valves to ensure they are functioning cor-

rectly and not leaking. It's crucial to maintain the tank properly to prevent potential

safety hazards due to overpressure or material failure.

## 4.4 Safety Precautions

Operating the HDPE Bottle Pre-Cleaning Station involves various components that re-

quire careful handling to ensure safety. Pay special attention to the following:

- Protective Gear: Always wear appropriate protective gear, including gloves, eyewear,

and closed-toe shoes, to safeguard against potential hazards such as splashes, sharp

edges, or falling tools.

- Handling Sharp Edges: The cutting tool incorporates sharp blades that pose a risk of

cuts or injuries. Handle the cutting module with utmost care, especially when inserting

or removing bottles from the adapter. Ensure the blades are fully retracted when per-

forming maintenance or adjustments.

- Monitoring Water Pressure: The pressure tank is a critical component of the cleaning

module. Regularly check the tank's integrity and the pressure levels during operation

using the barometer and a visual check on deformed parts or leakage. Ensure that the pressure stays within the recommended safety limits to prevent any risk of tank rupture

or leaks. For this reason do not operate the pre-cleaning station without a safety valve.

- Secure Operation Area: Keep the operational area around the pre-cleaning station

clear of clutter, water, and cleaning agents to prevent slips and falls. Ensure that all

pipes and hoses are properly managed to avoid tripping hazards.

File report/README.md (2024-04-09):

<!-- badges: start -->



<!-- badges: end -->

<h1> Design of an HDPE bottle collection and pre-cleaning system for recycling in Blantyre, Malawi </h1>

<b>Contributors</b>  
- Timo Stutz *author*  
- Elizabeth Tilley <a href="https://orcid.org/0000-0002-2095-9724">
ORCID logo 0000-0002-2095-9724
</a> *supervisor*  
- Lin Boynton <a href="https://orcid.org/0000-0002-9944-3834">
ORCID logo 0000-0002-9944-3834
</a> *supervisor*  
- Jakub Tkaczuk <a href="https://orcid.org/0000-0001-7997-9423">
ORCID logo 0000-0001-7997-9423
</a> *supervisor, developer, maintainer*  
- Nicolas Seemann-Ricard <a href="https://orcid.org/0000-0002-0945-7475">
ORCID logo 0000-0002-0945-7475
</a> *developer*  

<br>
<p align="middle"> 

<br><br>
This work is certified by the Open Source Hardware Association.  

<br>
**The complete description of the system design, its functionalities, and  is available on:  
[Github pages](https://global-health-engineering.github.io/pre-cleaning-system-design-for-HDPE-bottles/).**  
It compliments the openly-accessible master’s thesis, available on  
the [ETH research collection](https://doi.org/10.3929/ethz-b-000658745).  
The pdf version of this repository is available in the [`report` directory`(report/).
</p>

# Background

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

# License

This work is licensed under
[Creative Commons Attribution 4.0 International](https://github.com/Global-Health-Engineering/pre-cleaning-system-design-for-HDPE-bottles/blob/main/LICENSE.md).

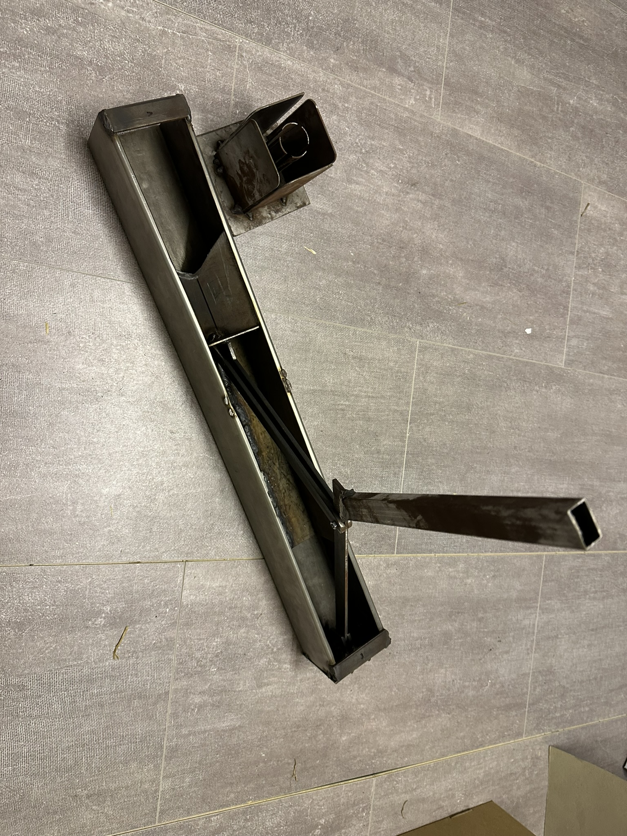
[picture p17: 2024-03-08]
img/additional_media/prototype/open_cutting_module.JPEG

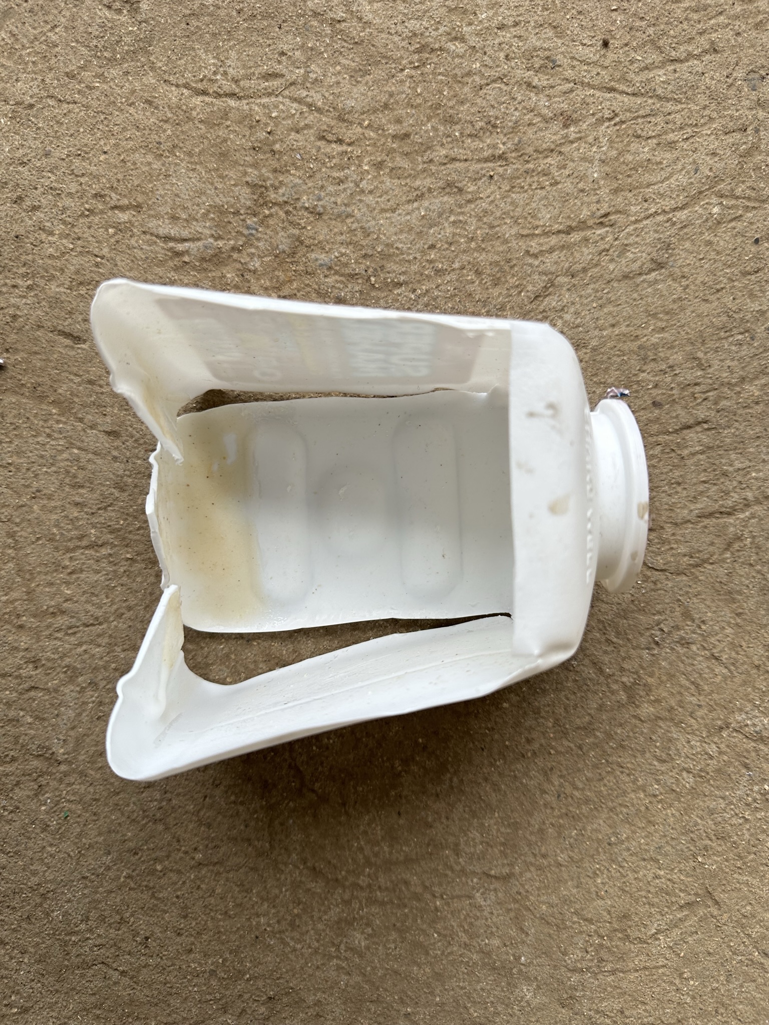
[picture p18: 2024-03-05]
img/additional_media/prototype/cleaned_and_cut_bottle.jpeg

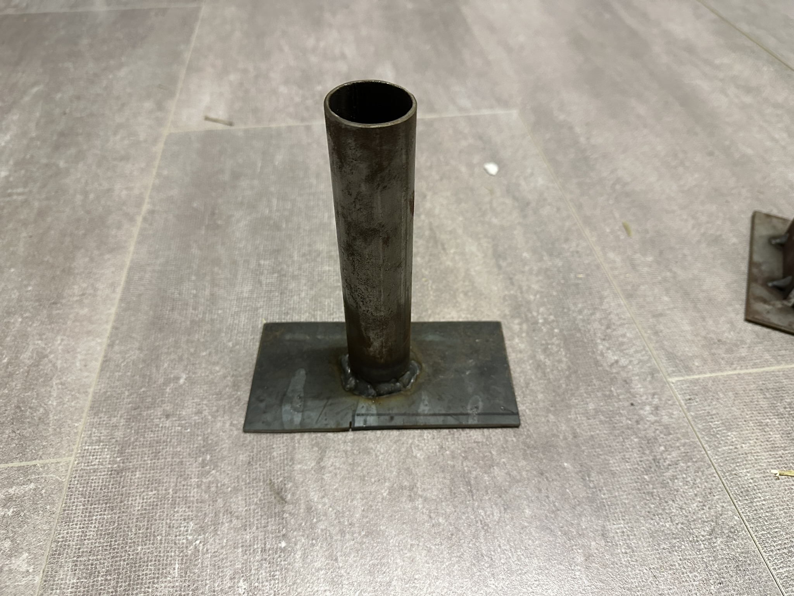
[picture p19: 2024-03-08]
img/additional_media/prototype/inflation module.JPEG

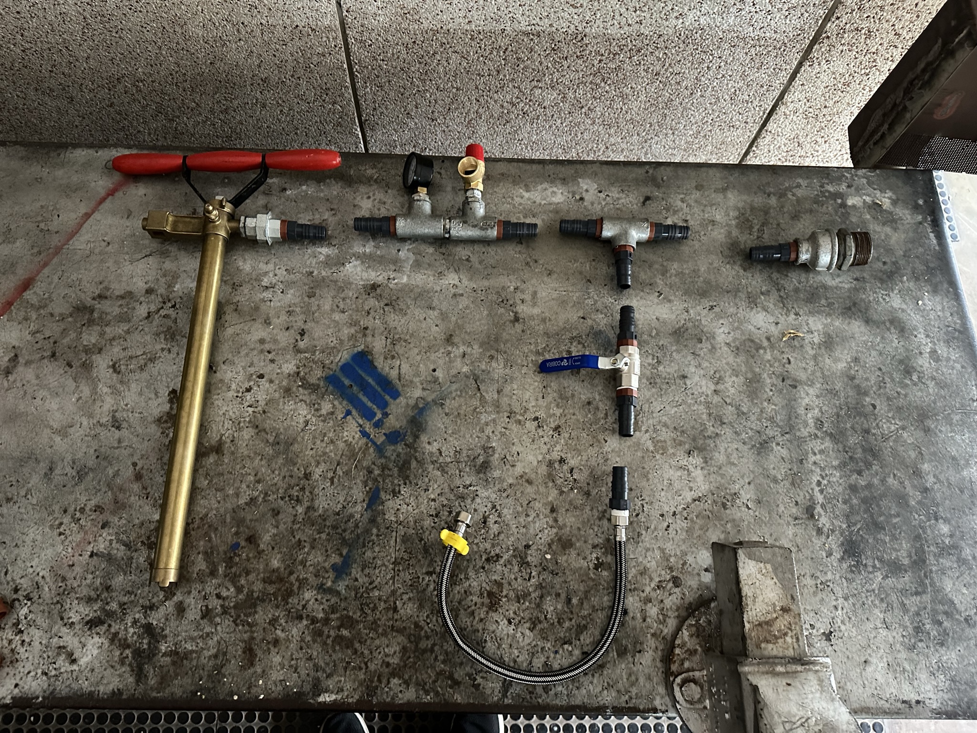
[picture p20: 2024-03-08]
img/additional_media/prototype/laid_tubing.JPEG

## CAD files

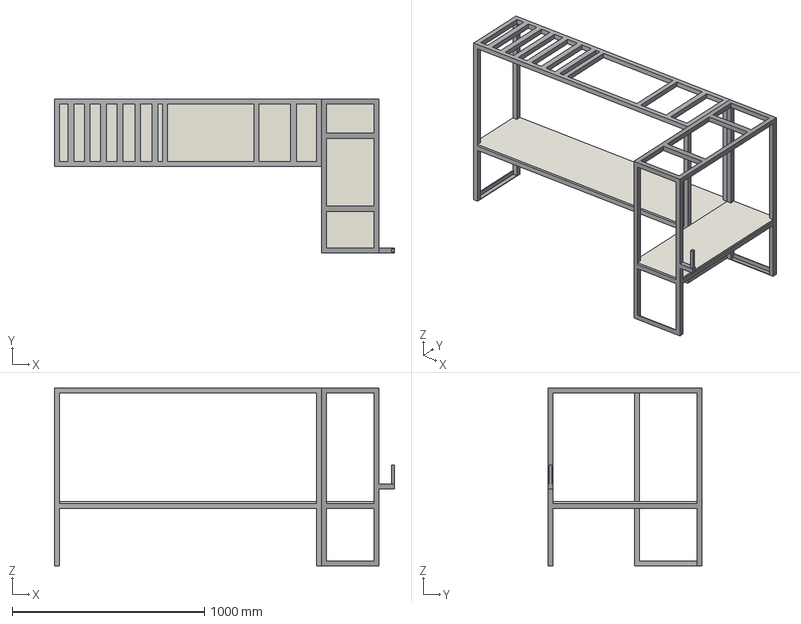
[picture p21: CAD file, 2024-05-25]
CAD/frame_workbench.step
1769.6 x 800.0 x 925.4 mm

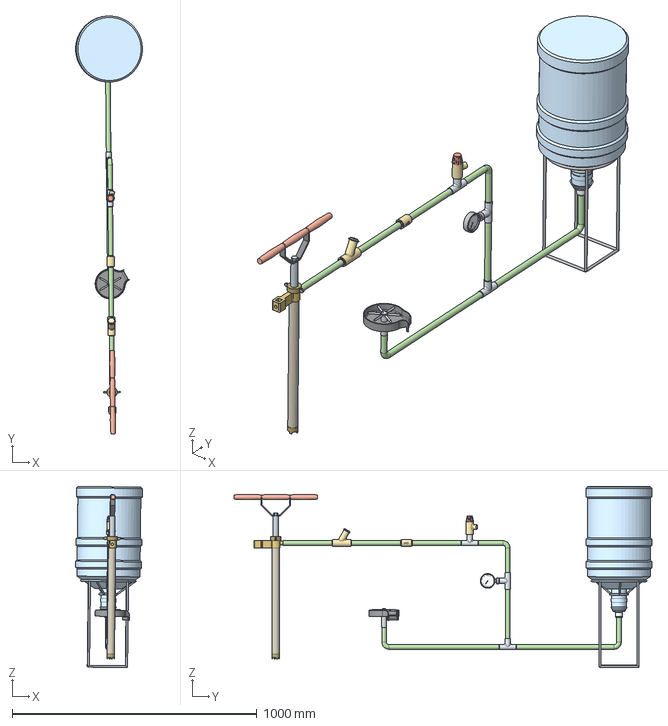
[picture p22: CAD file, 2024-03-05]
CAD/water_module.step
273.5 x 1708.8 x 741.0 mm

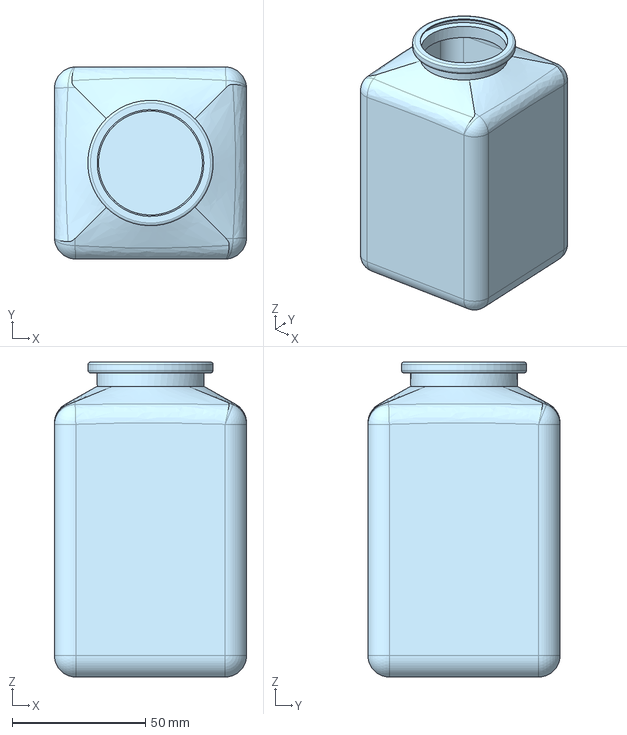
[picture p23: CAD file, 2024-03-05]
CAD/super_maheu_bottle.step
72.0 x 72.0 x 118.1 mm

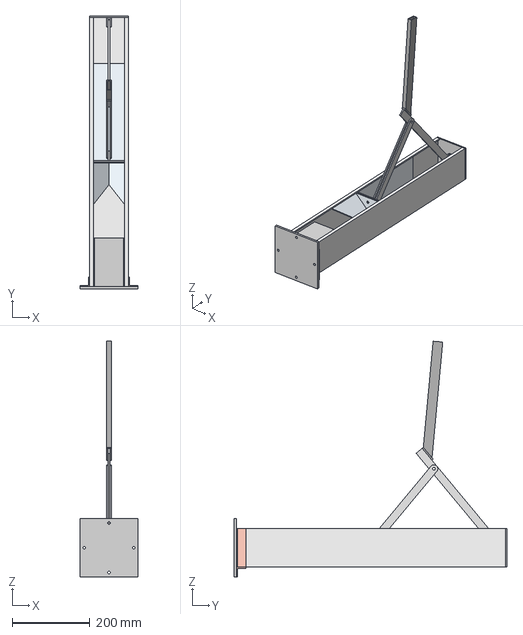
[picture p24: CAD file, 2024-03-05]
CAD/cutting_tool.step
150.0 x 704.0 x 607.8 mm

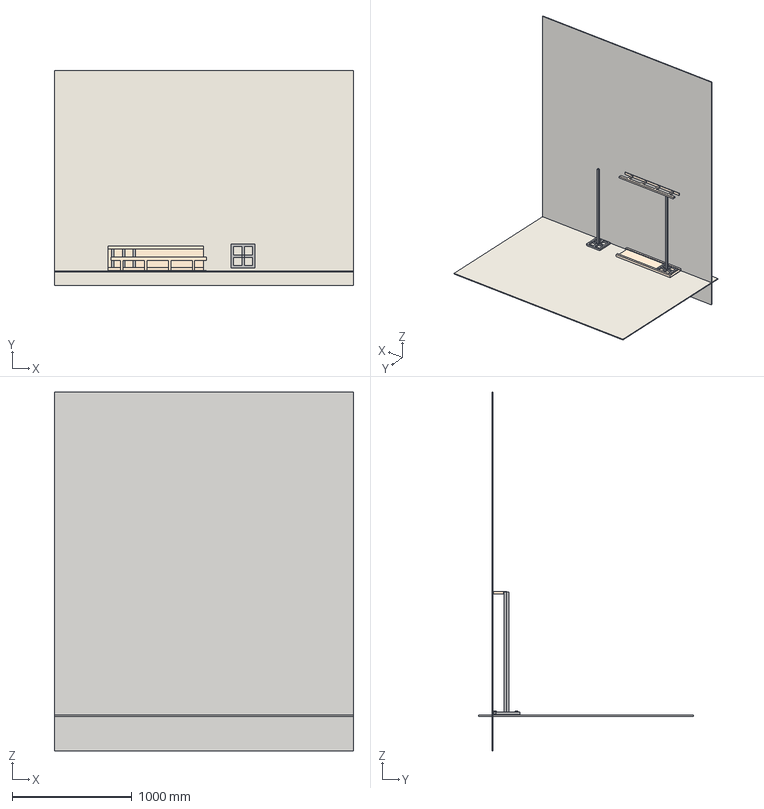
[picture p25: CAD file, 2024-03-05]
CAD/truck_rail.step
2501.8 x 1800.0 x 3000.0 mm

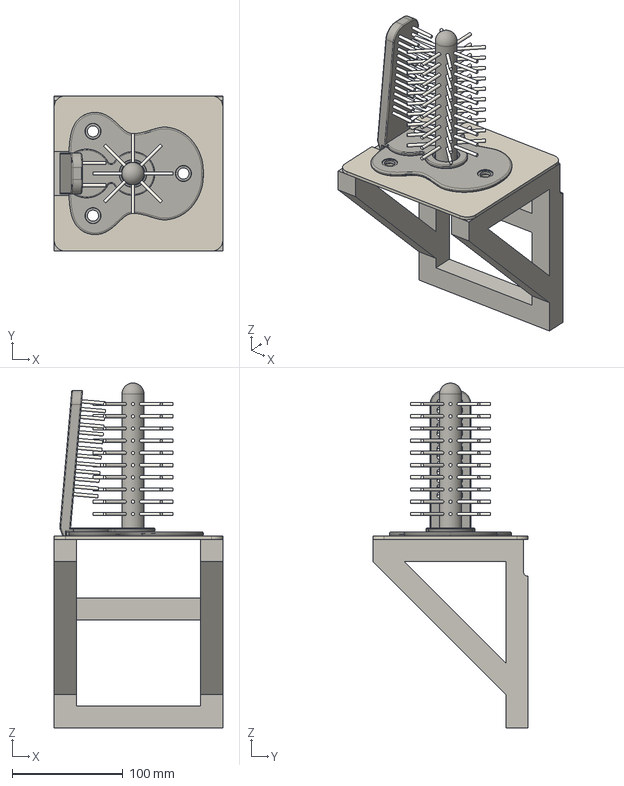
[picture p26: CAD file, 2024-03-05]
CAD/brush.step
152.0 x 140.0 x 310.9 mm

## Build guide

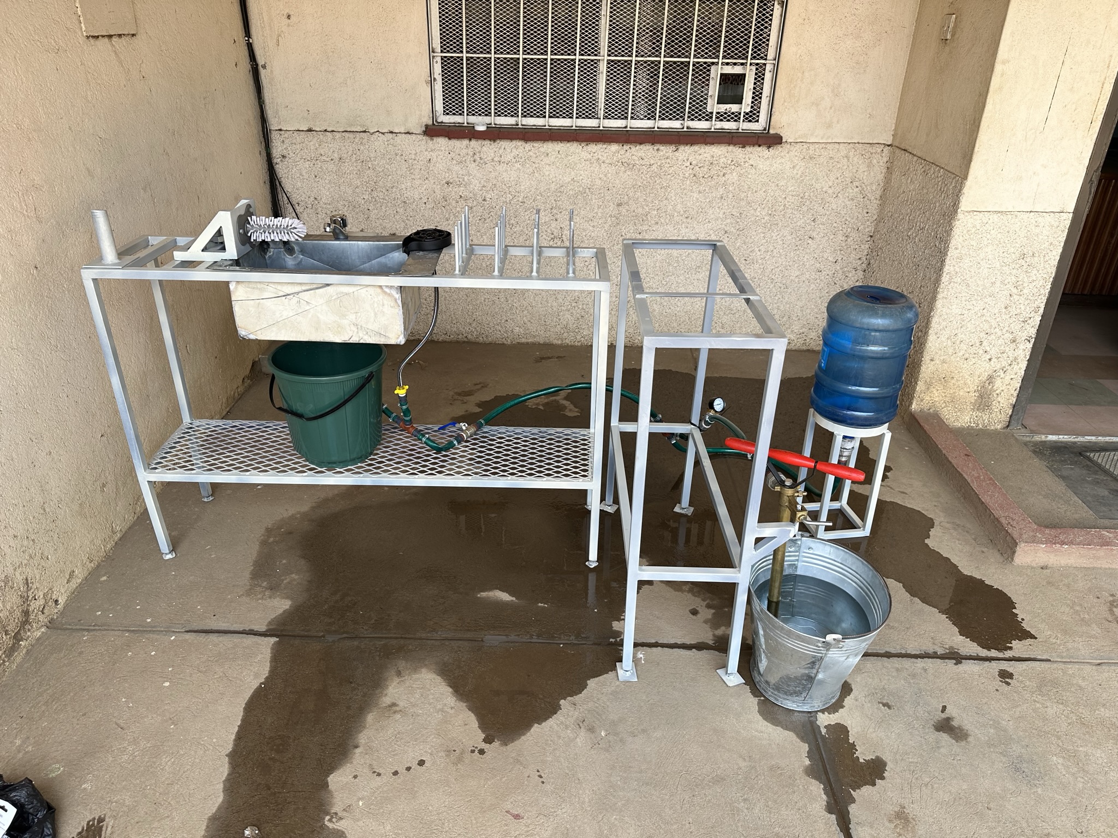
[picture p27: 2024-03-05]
img/additional_media/prototype/complete_assembly_photo.jpeg

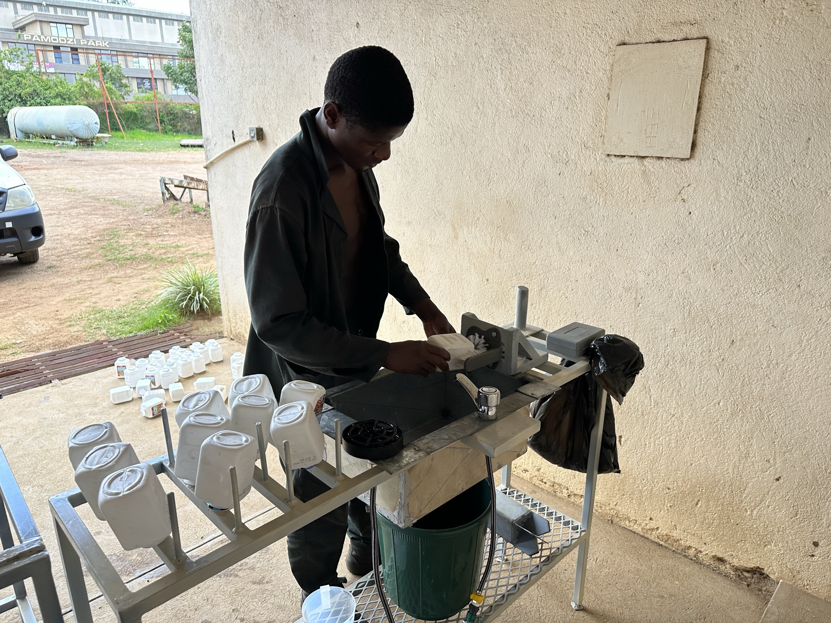
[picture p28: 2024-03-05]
img/additional_media/prototype/station_in_operation.jpeg

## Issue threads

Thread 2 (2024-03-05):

suggest changes to content/structure

jaktk, 2024-03-05:
Hi Lars, this repo is there to share Timo's hardware design. I started putting together its conent. If you have any suggestions, please suggest or commit them into a branch.

Together with Nic, we figured out it does not make too much sense in using the Open Hardware license as it is quite specific to electronic harware design. I would just go with our standard CC-BY-4.0.

larnsce, 2024-03-05:
Thank you, @jaktk. This is exciting. Thank you for doing the research on licensing, good to know that CCBY works.

On content and structure:

- Keep the landing README.md short and to the point, if you write up a more comprehensive handbook, do that separately and link it
- Have a look if you can find other examples of best practices for setting up open source repositories for hardware. Have you seen this? https://github.com/aolofsson/awesome-opensource-hardware  (more details: https://www.perplexity.ai/search/What-are-best-eYt395oZQu.ZcB15YuS_Jw#1)

On archiving and citation.

- Use the Zenodo GitHub integration for archiving on Zenodo and DOI generation. I would say that's the most important part.
- Then add the DOI to your CITATION.cff
- Once you are done, import the entry using the DOI to the ETH Research Collection

Addition to our GHE website:

- we will need a new category "Designs" under "Publications" https://ghe.ethz.ch/publications.html

jaktk, 2024-03-06:
Thanks @larnsce, I've seen those repos, at least part of them. My problem with them is that they are very electronics-focused (where actually OHRW license would be a good option).

There is an open sprinkler project: https://github.com/OpenSprinkler where they cover both software and hardware (limited to cad drawings). However, the hardware part of this repo is much less developed compared to the software version and I somehow understand it - these are just the cad files.

To sumarize, I haven't found something very very relevant which would change my view on it. One example which I like (from NASA) is here: https://github.com/nasa-jpl/open-source-rover . But again, that's a repo where hardware development (i.e., frame, wheels) is important of less importance compared to electronics.

Regarding the README structure, do you have an example? I was used to writing everything in the main readme actually, sort of like with one of your repos: https://github.com/Global-Health-Engineering/durbanplasticwaste

Regarding citations, that's pretty clear. The only point which we should discuss is whether this should be imported as a seprarate entry to the ETH research collection or rather a supplementary information to the manuscript, just like in case of Dominic Waltti's work: https://www.research-collection.ethz.ch/handle/20.500.11850/646138

larnsce, 2024-03-07:
> The only point which we should discuss is whether this should be imported as a seprarate entry to the ETH research collection or rather a supplementary information to the manuscript

As a separate entry. Then, still add it as supplementary information anyways. It will increase it's discoverability a lot by being a separate entry. I would also suggest to do that for students going forward.

jaktk, 2024-03-07:
Thanks, Lars.

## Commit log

2024-03-05 add photo of the assembly
2024-03-08 Folder reorganization and adding media
    [assembly_workbench.step, brush.step, complete_assembly.step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]
2024-04-05 readme and folder structure
    [assembly_workbench.step, brush.step, complete_assembly.step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]
2024-04-09 update github pages
    [assembly_workbench.step, complete_assembly.step]
2024-04-09 Add DOI, add theme, add contact elements
    [assembly_workbench.step, complete_assembly.step]
2024-05-25 add frame cad file
    [assembly_workbench.step, frame_workbench.step]

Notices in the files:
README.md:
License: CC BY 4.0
